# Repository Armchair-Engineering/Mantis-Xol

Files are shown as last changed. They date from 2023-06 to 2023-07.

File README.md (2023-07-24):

# Mantis Xol 2 is now [Xol-Toolhead](https://github.com/Armchair-Engineering/Xol-Toolhead)
## We have moved over to a [new home](https://github.com/Armchair-Engineering/Xol-Toolhead) and made some big updates which will make the toolhead much easier to use, maintain, and build.
Go to [https://github.com/Armchair-Engineering/Xol-Toolhead](https://github.com/Armchair-Engineering/Xol-Toolhead) and check it out.

<br/> 
Everything seen below here, and still in this repository is now an archive.

___

## Mantis Xol 2 [ARCHIVE]


### Description
Originally a project to slap 5020 blower fans onto Mantis, this toolhead variant started as an attempt to improve parts cooling, spurred on by Derpimus' noted cooling woes on his DOOMCube. After finding that the 5020s were just plain too fat to fit without looking like a standard Ender 3 Thingiverse special, I abandoned the large fan dream in favor of better cooling efficiency and lighter weight. This new and improved dream was also corrupted by my then budding and now all-consuming love for worm gears.

Join me on Discord (https://discord.gg/armchairengineeringsux)

### New Features for Xol 2
 - Cooler: Still a little ugly but better
 - Lighter: 260g-ish for Sherpa Mini
 - Rigid-er: I want to throw this thing across the room

##### Features:
 - Better airflow than Stealthburner (6-7 CFM through short ducts vs 4.6-5.2 CFM through long ducts)
 - Improved resonance management compared to Mantis 5015
 - Support for Sherpa Mini-pattern extruder mounting as well as Annex Engineering's **Double Folded Ascender** worm gear extruder
 - Support for JosAr's Klicky, VinnyCordeiro and WhoppingPochard's PCB Klicky, and Nionio6915's Euclid
 
##### Supported (incl. usermods/experimental):
|Hotends |Extruders |Probes |
|--- |--- |--- |
| Rapido HF | Sherpa Mini | VoronDesign's TAP |
| Dragon SF/HF | Orbiter 2 | Beacon (normal) |
| Revo Voron | Vz-hextrudort | (PCB) Klicky |
| Phaetus XG | DropEffect | Euclid |
| Bambulab | LGX Lite |--- |
| Dragon UHF Mini / NF Crazy |--- |--- |
 
##### Future Development (No ETA):
 - Bracing for PCB mounts
 - Quickdraw 2 support
 - Update DFA Bottom to latest version for slightly better heatset quality of life
 - Port nozzle LEDs to Xol 2 (see usermods)
 - Port MMU sensor support to Xol 2
 - Confirm fitment for MattTheBaker's Beacon

### Build Notes:
This toolhead might require other modifications to retain full functionality of your printer. 
 - All test machines used for this mod had Rama's front idlers which have a much lower profile compared to stock Voron front idlers. The fan assemblies might conflict and reduce usable X travel.
 - The Klicky Probe carriage that was adapted was originally designed for the Dragon hotend. You'll need to use a taller probe body to reach the bed such as the one used by [Unklicky BFP](https://github.com/majarspeed/Unklicky). *This isn't an issue for Euclid or PCB Klicky*.
### Bill of Materials 
|Item|Count|Note|
|----|-|--|
|Rapido or XG|1|
|4010 24v blower fans|2|Add Polulu 3796 if you want the fancy 12v Deltas|
|2510 24v axial fan|1|
|M2x8 SHCS|2|
|M2x12 SHCS|4|
|M2x20 SHCS|2|
|M2.5x20 SHCS|4|
|m3x6 BHCS|7|
|m3x8 BHCS|7|
|m3x20 SHCS|2|
|M2 Heatset 4L x 3.5 OD|11|
|M3 Heatset "Standard"|10|
|D2F-5L Microswitch|1|
|M2x8 or M2x10 Self-Tapping|1|Optionally 1 more M2 heatset and an M2x8 SHCS|
|6x3 magnets|3|
|ZIP TIES||
### Changelog
#### 29 November 2022 - Beacon Support
- Release Day means Beacon Support. Find it in the Experimental folder.
#### 27 November 2022 - Tap Support
- Release Day means Tap Support. Find it in the Experimental folder.
#### 22 November 2022 -Revo Voron
- Added support for Revo Voron with the Sherpa Mini Hotend mount
#### 10 November 2022 - Shiny shiny
- Added nozzle LED support. Find it in the Experimental folder.
#### 23 October 2022
#### 3 October 2022 - Xol 2
- Improved aesthetics
- Downsized HE fan to 2510
- No more self-tapping screws
- Added front brace for Sherpa Mini
- New ducts for Tridents with lead screws
- Miscellaneous printability improvements
#### 3 Aug 2022 - Xol with Boots
- Added MGN9H carriages for PCB Klicky
- Added additional stabilization for ducts. Ideally, these are fastened with 2x M2x20 and M2 heatset inserts.


### Acknowledgement
[Long/Mandryd](https://github.com/mandryd/VoronUsers/tree/master/printer_mods/Long/Mantis_Dual_5015) for the Mantis toolhead.<br/>
[TheWarolf](https://github.com/TheWarolf/Voron-Personal-Mods/tree/main/V2/Long_Mantis_Toolhead) for the ERCF sensorized Hotend Mount.<br/>
[Derpimus](https://github.com/lraithel15133) for the exegesis, some CAD work, feedback, and just being a rad dude.<br/>
[KayosMaker](https://github.com/KayosMaker) for the MGN12 Klicky X-Carriage and CAN board mounts and spacers.<br/>
[JosAr](https://github.com/jlas1/Klicky-Probe) for Klicky.<br/>
[WhoppingPochard](https://github.com/tanaes) and [VinnyCordeiro](https://github.com/VinnyCordeiro/) for PCB Klicky.<br/>
[Nionio6915](https://github.com/nionio6915/Euclid_Probe) for Euclid. <br/>
[VoronDesign](https://github.com/VoronDesign) for this particular CoreXY flavor.<br/>
[AnnexEngineering](https://github.com/Annex-Engineering) for the Sherpa Mini and Double Folded Ascender extruders, and the K3 that influenced the air management of the ducts. And also for giving access to an early revision of the new DFA so it could be adapted for this toolhead.<br/>
[Clee](https://github.com/clee), you know what you did.  
[Takuya](https://github.com/T4KUUY4)... just added the 36mm SB2040 mount

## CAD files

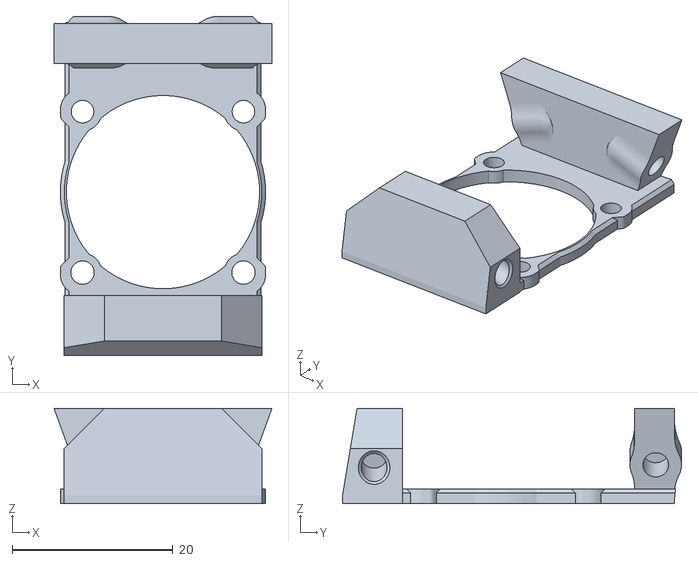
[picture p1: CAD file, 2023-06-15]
STL/Xol 2/TAP/Rapido/[a]_Xol 2 Rapido - Faceplate B.stl
27.1 x 42.1 x 11.8

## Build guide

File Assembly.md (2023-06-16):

# Assembly of YOUR NEW Mantis Xol 2 Toolhead

| Instruction | |
| --- | --- |
| Insert **M3** Heatset Inserts into the *Carriage* as indicated. For best results, insert almost completely with a soldering iron before finishing by pressing against a flat, heat resistant surface. |  Carriage M3 Heatsets |
| Insert **M3** Heatset Inserts into the *Hotend Mount* as indicated. Judicious use of the tip mentioned in the previous step will be helpful. | Hotend Mount M3 Heatsets  |
| Insert **M2** Heatset Inserts into the *Hotend Mount* as indicated. For the upper Heatset Inserts, you may use the table method if you're careful not to deform the plastic. For the lower Heatset Inserts, this is less recommended. You may use one of the M2x20s to ream the holes in Xol's boots as the displaced plastic may now act as an obstruction in a later step. |  Hotend Mount M2 Heatsets  |
| Insert **M2** Heatset Inserts into the faceplate as indicated. **Note:** The upper Heatset Inserts here are not flat against the plastic part. Attempting to use the flat surface tip mentioned in previous steps will ruin your day. Do your best to make the upper Heatset Inserts parallel to the lower. |  Front Plate M2 Heatsets  |
| Prepare the wiring for the Z probe of your choice. Follow instructions for your specific selection as provided in that solution's repo. The Heatset Insert tip may or may not be helpful during this step. | This image space left intentionally blank.  |
| Attach your hotend of choice (Rapido shown here) using the corresponding screws for your selection. For Rapido, ensure that your heater and thermistor wiring exit toward the rear left. There is no application for the aforementioned Heatset Insert tip during this step. |  Hotend Install |
| Attach the *Hotend Mount* to the *Carriage* as indicated, using M3X20 screws in the upper positions and M3x8 in the lower. **Note:** Don't crush your wiring. | Hotend Mount to Carriage  |
| Fasten the *Faceplate* and *2510 Hotend Fan* to the *Hotend Mount* with M2.5x20 screws as indicated. For XG, there will only be 2. Ensure that the *Hotend Fan* wiring exits toward the left as indicated. | Front Plate Assembly |
| Fasten the *4010 Parts Cooling Fans* to the *Hotend Mount* as indicated using M2x8 in the rear and M2x12 in the front.  | Top Blower Screws  |
| Fasten the *4010 Parts Cooling Fans* and attach *Ducts* as indicated using M2x20 in the rear and M2x12 in the front. For Tap installation, use M2x12 in the rear instead of M2x20 | Bottom Blower Screws and Duct Install  |
| Attach your selected *Extruder* with corresponding PTFE.  | This image space left intentionally blank.  |
| Secure your wiring with zipties.  | This image space left intentionally blank.  |
| You're done! Congratulations!  |  45 Degree Preview |

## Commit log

2023-06-15 STLs missing from TAP -> Rapido
    [a]_Xol 2 Rapido - Faceplate A.stl and [a]_Xol 2 Rapido - Faceplate B.stl missing from Rapido folder
    [[a]_Xol 2 Rapido - Faceplate B.stl]
2023-06-16 Update Assembly.md
    Duct installation note for Tap users - changed rear M2x20 to M2x12
